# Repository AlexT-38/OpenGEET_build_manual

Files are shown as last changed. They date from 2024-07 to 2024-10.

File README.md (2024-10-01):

# OpenGEET_build_manual

### About OpenGEET

OpenGEET is an open source implementation of Paul Pantone's GEET fuel preprocessor and emmisions reduction system. The goal of this project is to create a set *detailed and explicit* instructions for manufacture, installation and operation of the GEET system, for the purpose of reproducibility and independent validation.

### Project structure and format

The project will consist of:

* This repository
    * Drawings and STEP models of all custom mechanical parts
    * Fusion360 cad files - pending review of licences and personal data in exported files
    * Manufacturing and assembly notes
    * Run in and operation instructions
    * Schematics and PCB art for all custom electronics
* Firmware repository
    * Firmware for all microcontrollers used in the above
    * Programs and scripts for processing collected data
    * Firmware manuals

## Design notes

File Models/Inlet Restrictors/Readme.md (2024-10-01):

# Inlet Restrictors

Used to restrict airflow into the system and provide the correct operating vacuum in the reactor over a wide range of flowrates. A system for a single cylinder engine requires optimal geometry to maintain the required vacuum over the length of the intake stroke. A three or more cylinder engine can make do with flat restrictors, since airflow is mostly constant.

Optimal geometry has an elliptical inlet profile and a 60° conic outlet profile.

#### Profiles

* A - inlet profile ellipse has dimensions 2.0x1.2mm, outlet is a 118° cone
* A0 - inlet profile ellipse has dimension 2.0x1.2mm, outlet is a 60° cone

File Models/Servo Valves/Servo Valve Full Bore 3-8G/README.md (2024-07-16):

# OpenGEET Build Manual

## Servo Valve, Full Bore, 3/8" BSPP
#### 10/2023

To fit:
* Ball Valve: https://www.bes.co.uk/ball-valve-3-8-bsp-p-f-x-f-red-lever-handle-9688/
* Servo: Tower Pro MG996R https://www.towerpro.com.tw/product/mg996r/

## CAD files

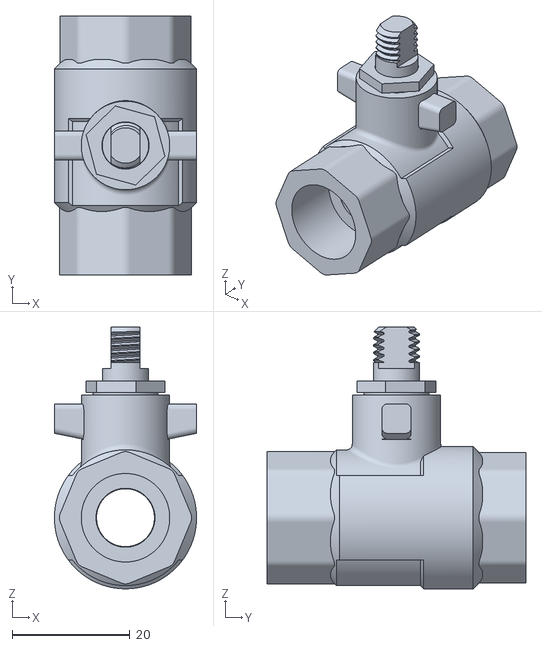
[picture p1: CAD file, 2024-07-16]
Models/Servo Valves/Servo Valve Full Bore 3-8G/Ball Valve 3-8th Full Bore.stl
24.1 x 43.9 x 44.4

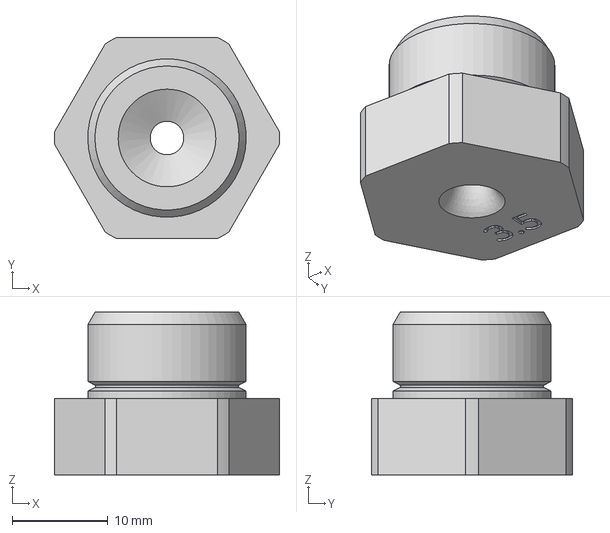
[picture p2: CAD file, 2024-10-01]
Models/Inlet Restrictors/G3-8 Venturi-3.5mm (fixed inlet shape).step
23.5 x 21.0 x 17.0 mm

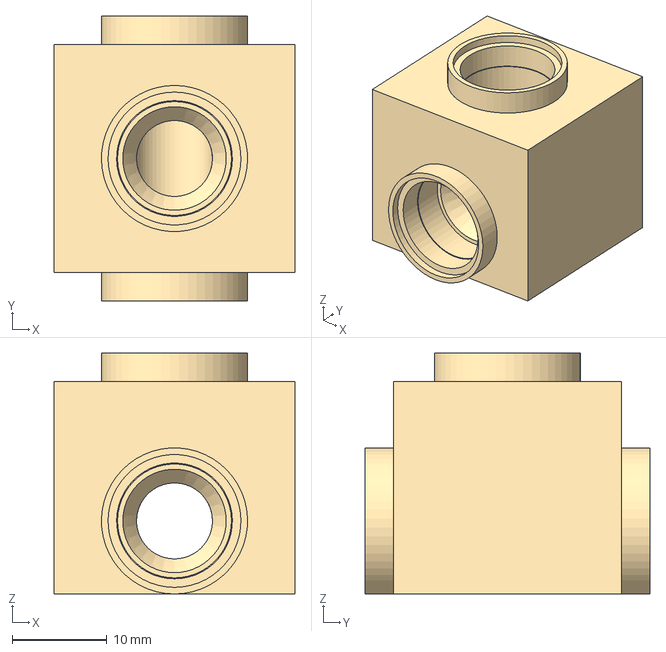
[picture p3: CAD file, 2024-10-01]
Models/Intake Manifold/Gas Mixing Venturi.step
25.4 x 30.0 x 25.4 mm

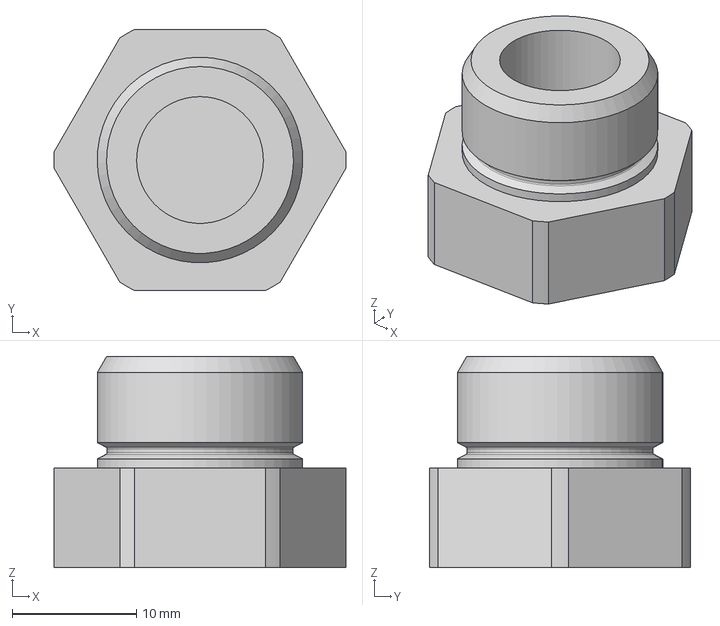
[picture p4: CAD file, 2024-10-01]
Models/Reactor/Plug.step
23.5 x 21.0 x 17.0 mm

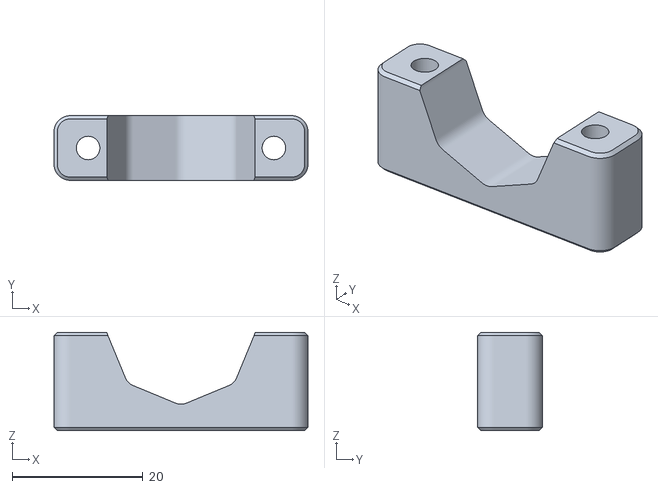
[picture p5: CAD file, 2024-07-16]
Models/Servo Valves/Servo Valve Full Bore 3-8G/Servo Mount Clamp Mk2.stl
38.8 x 9.90 x 15.0

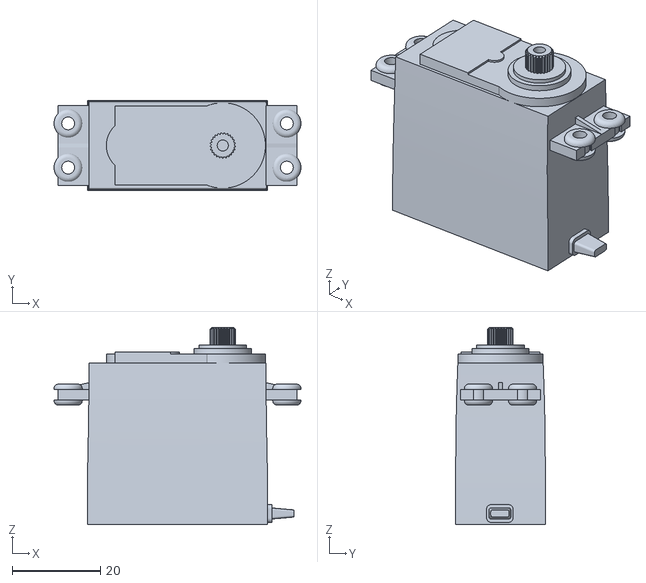
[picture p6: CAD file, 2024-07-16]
Models/Servo Valves/Servo Valve Full Bore 3-8G/Servo MG 996R.stl
55.9 x 20.3 x 44.6

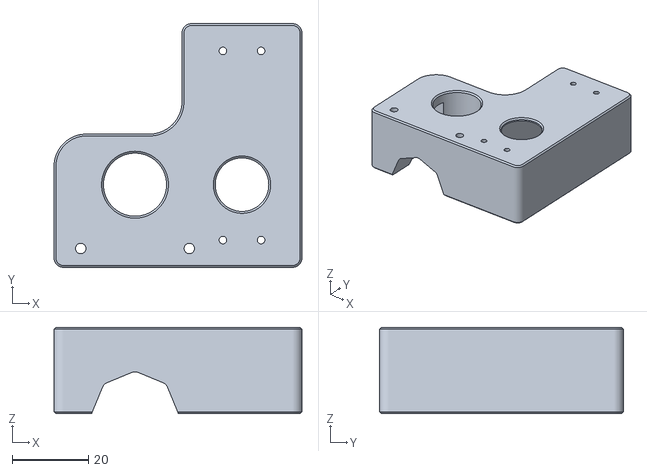
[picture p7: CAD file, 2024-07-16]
Models/Servo Valves/Servo Valve Full Bore 3-8G/Servo Mount Body Mk2.stl
64.9 x 63.8 x 22.6

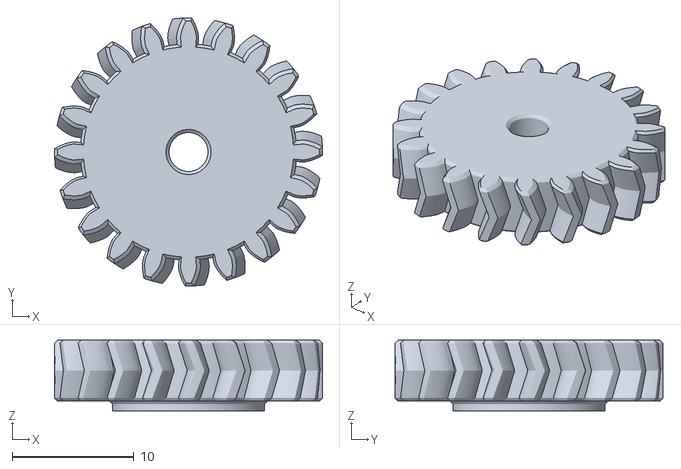
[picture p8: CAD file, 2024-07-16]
Models/Servo Valves/Servo Valve Full Bore 3-8G/Servo Gear.stl
22.0 x 22.0 x 5.80

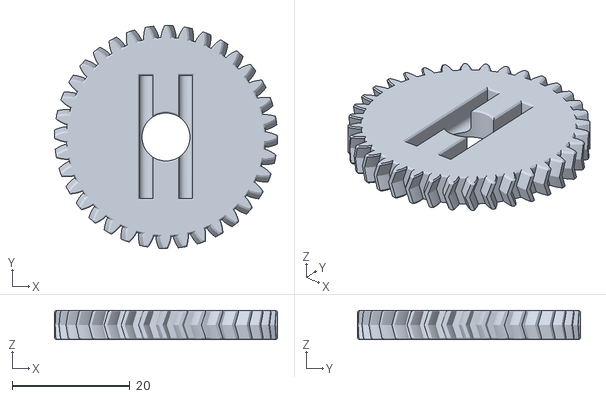
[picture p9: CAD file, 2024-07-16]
Models/Servo Valves/Servo Valve Full Bore 3-8G/Valve Gear.stl
37.9 x 37.9 x 5.00

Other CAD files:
Models/Inlet Restrictors/G3-8 Venturi Shape A CSA 18.9 - 4.90.step
Models/Inlet Restrictors/G3-8 Venturi Shape A CSA 23.3 - 5.45.step
Models/Inlet Restrictors/G3-8 Venturi-4.0mm (fixed inlet shape).step
Models/Inlet Restrictors/G3-8 Venturi Shape A CSA 10.0 - 3.57.step
Models/Inlet Restrictors/G3-8 Venturi Shape A CSA 3.47 - 2.10.step
Models/Inlet Restrictors/G3-8 Venturi Shape A CSA 8.09 - 3.21.step
Models/Inlet Restrictors/G3-8 Venturi Shape A CSA 2.80 - 1.89.step
Models/Inlet Restrictors/G3-8 Venturi Shape A CSA 2.27 - 1.70.step
Models/Inlet Restrictors/G3-8 Venturi Shape A CSA 12.4 - 3.97.step
Models/Inlet Restrictors/G3-8 Plug.step
Models/Inlet Restrictors/G3-8 Venturi Shape A CSA 4.28 - 2.34.step
Models/Inlet Restrictors/G3-8 Venturi Shape A CSA 5.30 - 2.60.step
Models/Inlet Restrictors/G3-8 Venturi Shape A CSA 6.55 - 2.89.step
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

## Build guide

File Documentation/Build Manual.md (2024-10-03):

# OpenGEET Build Manual

## General notes

The reactor will be installed vertically. Unprocessed fuel enters the reactor at the bottom and exits as Syn Gas at the top. Exhaust from the engine enters the reactor at the top and exits at the bottom.

Exhaust entering the reactor must be at the correct temperature and pressure. Temperature is controlled by setting the length of pipe work from the engine exhaust prot to the reactor exhaust inlet. Pressure is controlled by restricting flow at the reactor exhaust outlet.

Fuel entering the reactor must be a fine mist or dense vapour. For petrol/gasoline, the fuel to air ratio is around 1:5. The fuel/air mixture should be cool and at the correct vacuum, approx 0.5 atm.

A good vacuum seal for the reactor is vital. Leaks will at least cause lean running, at worst will prevent the reactor from operating.

The engine will run even if the reactor is not functioning. A running engine alone is not a sign of success.

Care must be taken to ensure gas flow paths are smooth and avoid sharp corners. Any rough surfaces, discontinuites and sharp corners will limit gas flow rates and reduce system performance. They may also cause unprocessed fuel to drop out of suspension and interfere with the reactor.

Magnetic alignment is important. The reactor must be assembled such that magnetic fields in the material align with the local geomagnetic field. Welds create strong magnetic fields in the material and can cause problems. Heat treating parts to above the Curie temperature and allowing them to cool in their installed orientations in an environment free of magnetic clutter may help.

Electrical conductivity is a concern. There must be a free path for electrons to flow through the reactor, feed pipe, gas mixer, engine and exhaust pipework back to the reactor. All parts in this loop should be made of metal. Any sealing compounds used should not insulate the joint. Specifically, PTFE tape should not be used on threads.

The design makes use of 12mm copper pipe. Unfortunately in the UK this is not a standard size and is only available from specialist plumping supply stores. It is available from BES.co.uk and for this reason, they are the prefered supplier for plumbing parts.

## Assembly overview

* Engine
* Reactor Assembly
    * Reaction Rod
    * Inner Tube
    * Outer Tube
    * Inner Tees
    * Outer Tees
    * Rod Support and Plug
    * Vacuum Monitor Ports
    * Sight Glass
* Intake Manifold Assembly
    * Manifold Adaptor and Vacuum Monitor Port
    * Gas Mixing Tee
    * Intake Valve
    * Intake Restrictor and Filter
    * Gas Delivery Pipe
* Exhaust Manifold Assembly
    * Manifold Adaptor
    * Connecting Pipe
    * Exhaust Inlet Pressure Monitor Port
* Exhaust Assembly
    * Muffler
    * Backpressure Adjustment Valve
    * Exhaust Outlet Pressure Monitor Port
* Fuel Delivery Assembly
    * Bubbler
    * Bubbler Feed Float
    * Bubbler Inlet Valve
    * Bubbler Inlet Restrictor
    * Fuel Feed Pipe

## Assembly Descriptions

#### Engine

A Honda GX120 or equivalent.

Remove the exaust, filter, carburetta and fuel tank.

#### Reactor Assembly

##### Outer Sub Assembly

Outer Tube is 3/4" x 150mm pipe with BSPT or NPT threaded ends. Remove the internal weld seam. Magnetic orientation of the tube is important, and should be aligned with the local geomagnetic field when installed.

Outer Tees are 3/4" malleable iron equal tees (plain, not nickel plated).

Outer Tees are fitted with 3/4"-1/2" reducer bushings with the inner thread bored out and honed. The bore must be cut after assmebly onto the tee, with the work centred on the tee's Outer Tube mating thread. This is the best we can do to ensure concentricity of the inner tube inside the outer tube. The face of the outer through port should be machined flat.

Outer Tees are fitted to the Outer Tube with the reducer bushings aligned.

All outer tube parts are assembled using red high temperature silicone RTV to seal the joints. Don't rely on tapered threads for sealing. Do not use PTFE thread sealing tape.

##### Inner Sub Assembly

Inner Tube is cold drawn seamless (CDS) mild steel tube, outer dia 17.5mm, wall 3.2mm, for an inner dia of 11.1mm, cut to a length of 317mm. The ends are given 3/8" BSPP threads and a 2.6x1.4mm (w/d) o-ring groove.

Red high temperature silicone orings, 14x2mm (ID/CS), are fitted to the inner tube's o-ring grooves.

The Inner Tube is passed through the Outer Tube and located by its o-rings inside the reducer bores. Again, magnetic orientation is important, and should be aligned with the local geomagnetic field when installed.

Inner Tees are 3/8" malleable iron tees (not nickel plated). Each port of the tee should be machined flat and square using the thread as reference. An o-ring groove should be machined into the face of each port. Currently a 19x0.75 counter bore on the outer and side ports, and a ~22x1.1mm face groove with a 7° taper on the inside wall for the inner port.

Inner Tube is clamped in place by the Inner Tees threaded against the Outer Tees.

All sealing should be performed by o-rings for the Inner Tube and Tees, but can be sealed with red silicone RTV if pressure/vacuum testing fails. O-rings at the top of the reactor must be of a high temperature type. Future revisions may use copper washers instead.

##### Reaction Rod

Reaction Rod is a length of mild steel, S275. Correct magnetic orentation is vital for this part.

The relationship between the outer diameter of the rod and the inner diameter of the Inner Tube controls the degree of vacuum in the reaction area and the maximum flow rate of fuel through the reactor.

The outer diameter should be tightly controlled and consistent over its length. The surface finish should be mirror like.

The length and nose profile are dependant on the fuel and installed orientation. Heavier grades of fuel require longer and blunter rods. European grades of petrol need a rod in the 90-95mm range, US gasoline is closer to 85mm.

The rear end of the rod is a shallow divet slightly smaller than the outer diameter. It can be cut with a standard drill, with loose tolerances on dimensions and surface finish.

##### Vacuum Monitor Ports

Ideally there should be two Vacuum Monitor Ports, one at each end of the reactor. These could be machined directly into the Inner Tees, or made from 3/8" BSP extenders. For now, only one port will be required, at the top of the reactor as an extension to the top most port.

##### Sight Glass

Sight Glass is connected to the top most port of the reactor. A more ideal set up for operation would be to have the syn gass delivery pipe connected directly to the top port, but we wwant to see what's going on at the top of the reactor.

When the reactor is operating, there should be a ball of plasma cupped in the divet on the tail end of the reaction rod. Spectographic analysis of the light from that plasma should give us great insight into the composition of syn gas. It's also a clear sign that the reactor is operating.

#### Intake Manifold Assembly

##### Manifold Adaptor and Vacuum Monitor Port

The GX120's intake port is D shaped. It has a plastic adaptor to transition to a circle, which doubles as a heat break to prevent the engine from heating the carburetta. This part must be replaced with an aluminum equivalent.

This is also as a place as any to place an intake vacuum sensor port. While not necessary, it will help in analysis and comparison with an unmodified engine.

##### Gas Mixing Tee

The Gas Mixing Tee mixes syn gas from the reactor with air drawn in through the Intake Valve. The Tee has a reduce bore and smooth transition so that it acts as a venturi pump, applying increasing vacuum to the syn gas feed pipe as the Intake Valve opens and admits more air. This helps maintain the correct operating vacuum in the reactor, since opening the intake valve would otherwise cause an increase in manifold air pressure.

The current design is machined from a block of brass and fitted with lengths of 12mm copper pipe, soft soldered into place. The restricted bore is 8mm in diameter (vs 10.1mm for the copper pipe).

##### Intake Valve

The Intake Valve is a standard 3/8" BSP full bore ball valve. For our purposes, the handle is removed and replaced with a 3D printed servo bracket.

While ball valves are not noted for their ability to fine control flow rates, they do a good job of sealing when closed and are readily available from plumming suppliers.

The Intake Valve is fitted with an Intake Restrictor and a 12mm compression fitting on the other, both with o-rings to ensure air-tightness.

##### Intake Restrictor and Filter

The Intake Restrictor is a brass 3/8" BSPP plug with a contoured hole.

The size and profile of the hole needs to be matched to the engine. The profile should be eliptical on the outside and conic on the inside. This profile offers optimal flow rates over a range of vacuum levels. This is important for single cylinder engines as the intake flow is discontinuous. Increasing the range of flow rates over which vacuum can be maintained increases the range in which the reactor is operating, and improves performance.

Filtering is optional, but will reduce engine wear from ingested particulates.

#### Exhaust Manifold

##### Manifold Adaptor

##### Connecting Pipe

##### Exhaust Inlet Pressure Monitor Port

#### Exhaust Assembly

##### Muffler

##### Backpressure Adjustment Valve

##### Exhaust Outlet Pressure Monitor Port

#### Fuel Delivery Assembly

##### Bubbler

##### Bubbler Feed Float

##### Bubbler Inlet Valve

##### Bubbler Inlet Restrictor

##### Fuel Feed Pipe

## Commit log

2024-07-16 Added Full Bore 3-8G Servo Valve Models
    [Ball Valve 3-8th Full Bore.stl, Servo Gear.stl, Servo MG 996R.stl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]
2024-07-21 Create Ball Valve Servo Mount 3-8th Full Bore Mk2.step
2024-10-01 Added Inlet Restrictor and Gas Mixer Models
    Plus updated folder structure and readmes.
    [G3-8 Plug.step, G3-8 Venturi Shape A CSA 10.0 - 3.57.step, G3-8 Venturi Shape A CSA 12.4 - 3.97.step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]
2024-10-03 Create Build Manual.md
    Added some general notes, and overview of the assemblies and a brief description of the assemblies up to Exhaust Manifold Assembly
